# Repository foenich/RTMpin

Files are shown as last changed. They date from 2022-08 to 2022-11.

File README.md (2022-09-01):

# RTMpin
This is a pinball project.

A Rollergames playfield was turned into a hybrid pinball machine (pinball firmware via PinMAME like in virtual pinball, but with real playfield and steel balls).

The emulator PinMAME runs on a Raspberry Pi and controls sound, DMD and a few IO-boards underneath the playfield. These in turn read the switch positions and activates the coils and lamps.

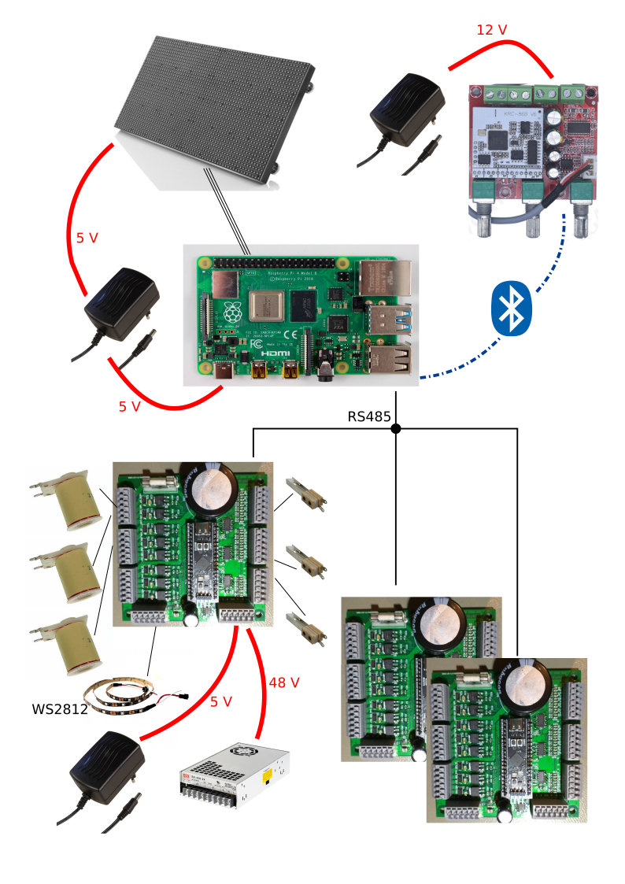
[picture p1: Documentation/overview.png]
overview


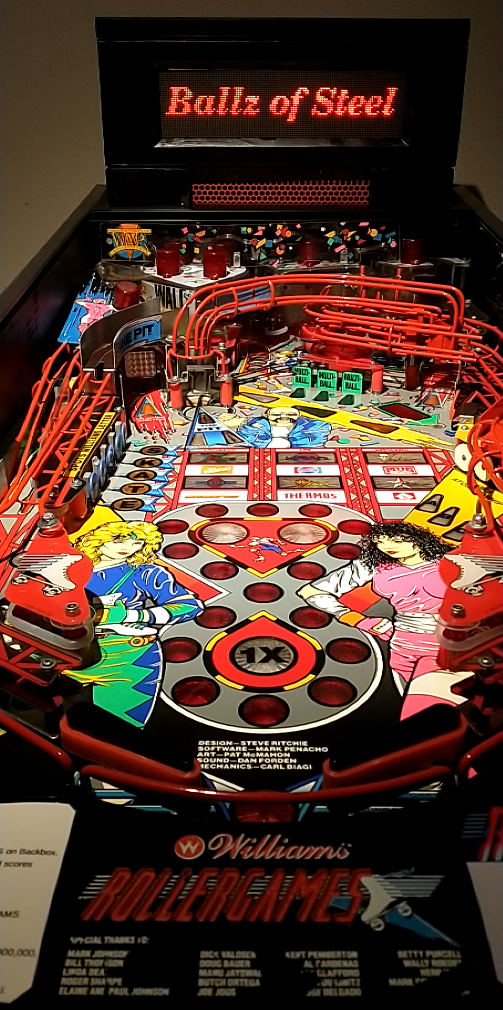
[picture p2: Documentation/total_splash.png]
Playfield and DMD


To watch a video see documentation folder: rg1stgame.mp4

A word of warning: this is a private, non commercial hobby project. Hardware and software still has errors (see issues and Changes.txt). To make use of anything of this project a basic understanding of electronics and programming is necessary. Nothing of it is "plug and play". I'm surely not liable for any damage to assemblies, pinball machines or even persons.

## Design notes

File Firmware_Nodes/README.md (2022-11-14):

# Firmware for IO boards
Firmware is written and compiled with STM32CubeIDE.

For now every node has it's own firmware: 3 nodes -> 3 firmware folders. As different machines can be run on the same playfield (and therefore the same nodes) an extra subdirectory was created for every machine. (e.g. RollerGames for the RG playfield with the RG game-code. Additionally the JudgeDredd_on_RollerGames for the RG playfield with the JD game-code and mapping)

Another folder contains the bootloader firmware witch is the same for all nodes.

Furthermore there are Python (V3) scripts for updating the nodes from the Raspberry Pi.

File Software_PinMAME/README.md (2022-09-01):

# Software related to PinMAME
A few files from the PinMAME project were adapted to communicate with the IO-boards (mainly s11.c).

Here is the link to the branch RTMpin (forked from PinMAME-Version of 5th of April 2021) and added neccessary changes for RTMPin  
https://github.com/foenich/pinmame/tree/RTMpin

Here is the link to the PinMAME project:  
[https://github.com/vpinball/pinmame](https://github.com/vpinball/pinmame)  

To make the DMD (Dot Matrix Display) running the excellent and well documentated library rpi-rgb-led-matrix was used:  
[https://github.com/hzeller/rpi-rgb-led-matrix](https://github.com/hzeller/rpi-rgb-led-matrix)  
To compile the RTMpin branch of PinMAME you also have to compile the rpi-rgb-led-matix library and make it visible to the system (e.g. copy librgbmatrix.so.1 and/or librgbmatrix.a to /usr/local/lib and run ldconfig)

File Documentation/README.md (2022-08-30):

# Technical Description RTMpin

## Overview
The emulator PinMAME runs on a Raspberry Pi and controls sound, DMD and a few IO-boards underneath the playfield. These in turn read the switch positions and activates the coils and lamps.

overview

## Electronics
The heart is a Raspberry Pi 4, which is connected to:
* LED-Matrix (DMD) via the digital I/O pins of the Raspi. 
* Audio amplifier via Bluetooth
* IO boards (nodes, underneath the board) via serial bus connection RS485

The LED matrix is a purchased part, as is the audio amplifier (Class D, 2 x 15 W for speakers in the backbox plus 30 W for the subwoofer in the cabinet). The IO-boards (nodes) are selfmade.

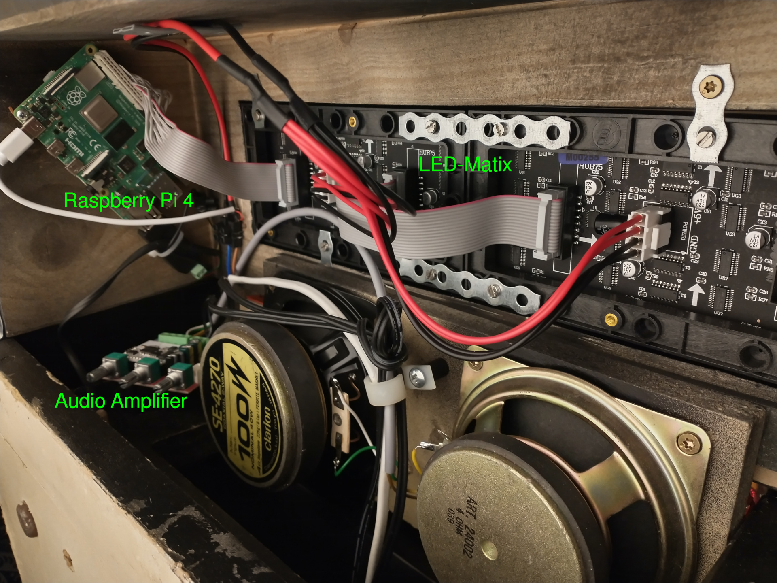
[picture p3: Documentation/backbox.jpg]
backbox


### IO-boards (nodes)
Each of the IO-boards (IO stands for Input/Output) can switch 8 high current outputs, read 18 inputs (direct inputs, no matrix circuitry) and drive a LED strip with WS2812 RGB LEDs. This is used to do all the lights under the playfield and the GI. For the Rollergames 3 IO-boards were necessary (actually 4 would be necessary, but to save a node I did it without the 3 control buttons for the menu navigation. At the moment I make these settings on the computer and then copy the corresponding file to the Raspberry. Maybe I'll add the switches to the IO's of the Raspberry, if I miss them).

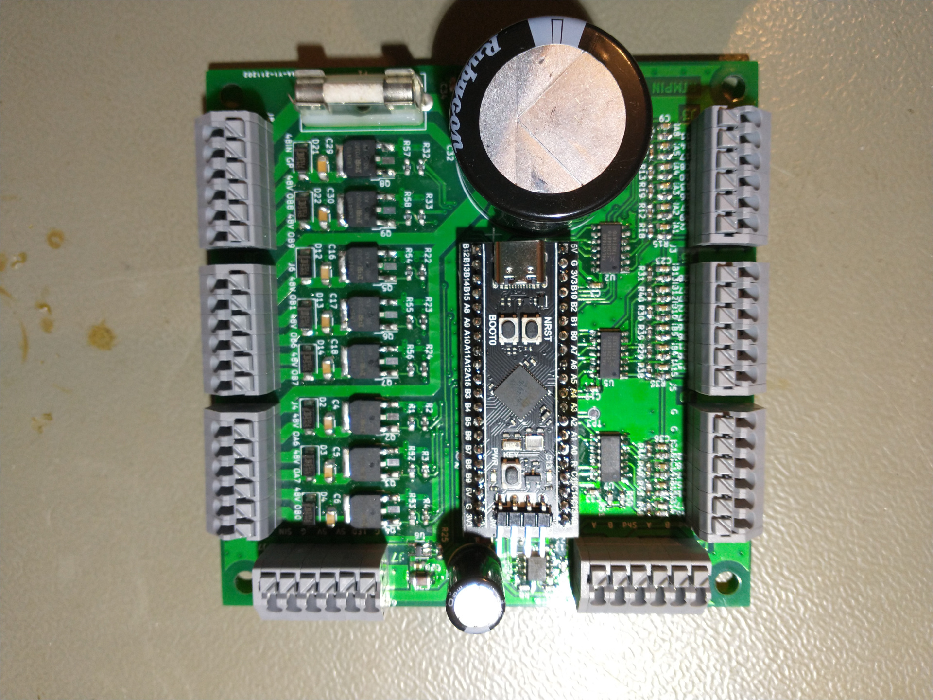
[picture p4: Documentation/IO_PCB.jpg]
Node


The control of the inputs and outputs and the communication with the Raspberry Pi is done by a STM32F401. I used a small board (Blackpill) for this, because it was better available than the microcontrollers themselvs (they were not at all available when I developed the board).

### Data communication
For communication with the Raspberry Pi I decided to use the serial bus connection RS485 (half duplex, 115 kbit/s). This is very robust (resistant to electro magnetic interference, EMI) and requires only two lines (plus a reference ground if necessary).

### Wiring
The wiring of the lamps is quite straightforward, since all LEDs have a small controller on board, which takes it's data packet from the serial data stream and passes the rest on to the next LED. Therefore only one wire for the data plus two wires for the power supply are needed.

For the wiring to the coils I used a 2-wire line per coil. This has significant advantages for electromagnetic compatibility (EMC), because the forward and return conductors are close to each other and thus emit less interference. Due to the distributed nodes on the bottom side of the board, the overall wiring is "mostly harmless".

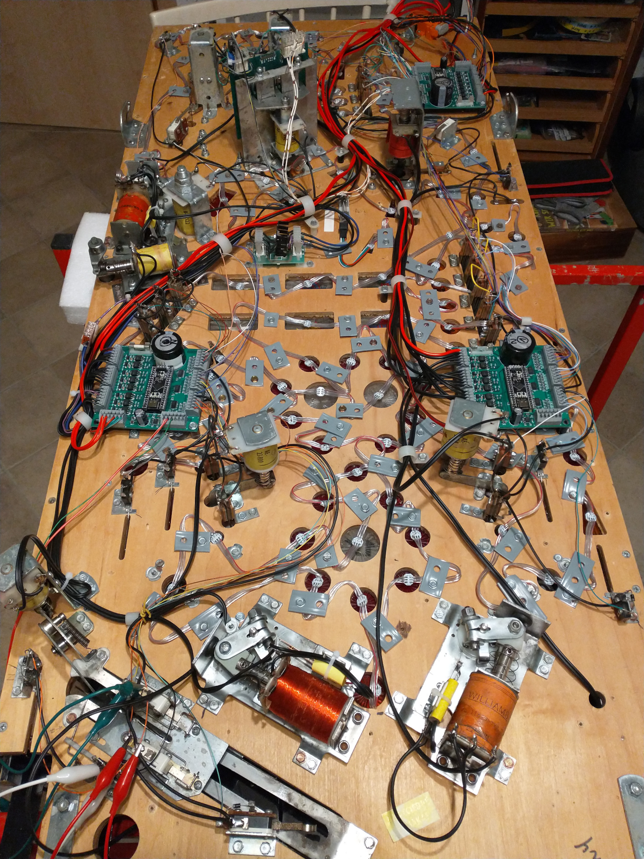
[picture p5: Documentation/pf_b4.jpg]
Overall wiring


### Power supply
The power supply for the components is made by 4 purchased power supplies:
* 5 V, 2.5 A for Raspi and DMD.
* 5 V, 2.5 A for node electronics and lamps
* 48 V, 7.3 A for the coils and flasher
* 12 V, 2 A for audio (I don't need the full power of the amplifier)

The two 5 V power supplies could be combined by a stronger single power supply, but I already had the wall power supplys at home, so they were used.

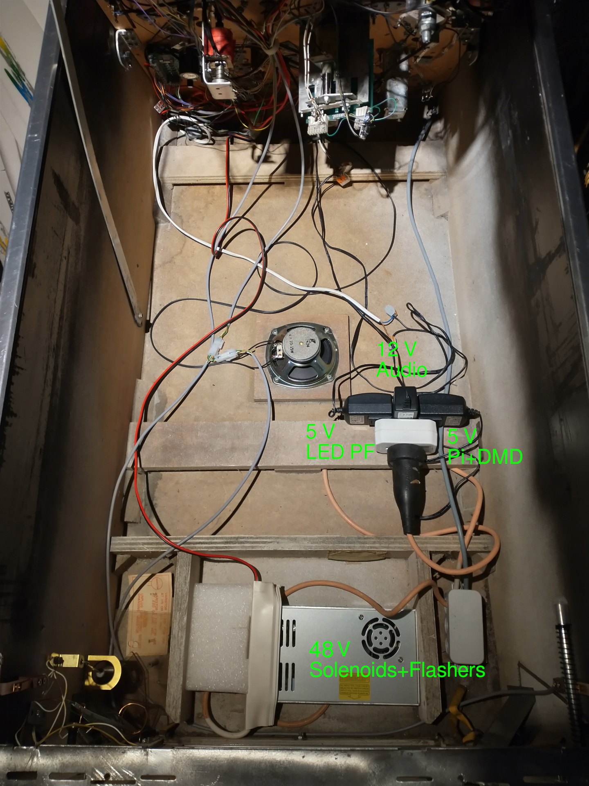
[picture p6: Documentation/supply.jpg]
power supply


## Software
### PinMAME
The linchpin of the software is the pinball emulator PinMAME:  
[https://github.com/vpinball/pinmame](https://github.com/vpinball/pinmame)  
The development team did a great job here and even ported the software to Linux, which makes it possible to control the pinball via a Raspberry Pi in the first place.

The pinball emulator runs on the Raspberry Pi 4 under a headless Linux (Raspberry Pi OS Lite). I had to make some adjustments to PinMAME for controlling the DMD and communicating with my IO boards (which lamps and coils are currently active and also for reading back the current switch states). 

### RPI RGB LED matrix
To control the DMD I used the excellent and well documented library from H. Zeller:  
[https://github.com/hzeller/rpi-rgb-led-matrix](https://github.com/hzeller/rpi-rgb-led-matrix)

### Firmware for IO boards
The software for the nodes was created with the development environment from ST Microelectronics for the STM32 family in C programming language. This went quite well, but as it was only a "prove of concept", I hardcoded many parameters and structured the code as simple as possible. I paid special attention to short interrupt routines and continuous (without waiting times) loop-based instruction sequences (similar to PLC programming). This is the only way to achieve the fast data sequences (almost 1 MHz) for the LED strips, which must be done in parallel to the RS485 transmission (115 kBaud) and in parallel to the IO control.

About all 60 ms the IOs (inputs and outputs) are updated by PinMAME. This is too slow for some functions. Therefore e.g. the flippers, bumpers and sling shots are controlled directly by the nodes. Here the delay time is shorter than one millisecond and therefore negligible.

All coils and flashers are powered with 48 V, so I only need one power supply for the power outputs. However, not all coils (and certainly not the flashers) are designed for 48 V, so all outputs are pulse width modulated (PWM). Therefore the time-averaged (and thus relevant) supply voltage for each coil and flasher can be adjusted individually.

The software for the IO boards can be updated directly from the Raspberry Pi. To do this, you can log in remotely (via ssh) to the Raspberry Pi and then start the software update. Very convenient - in my opinion - since you don't even have to open the pinball machine. The only data connection from the Raspi to the nodes is the RS485 bus. So the software update has to run over it, too. The process and the data transfer on the Raspberry side was realized via Python scripts.

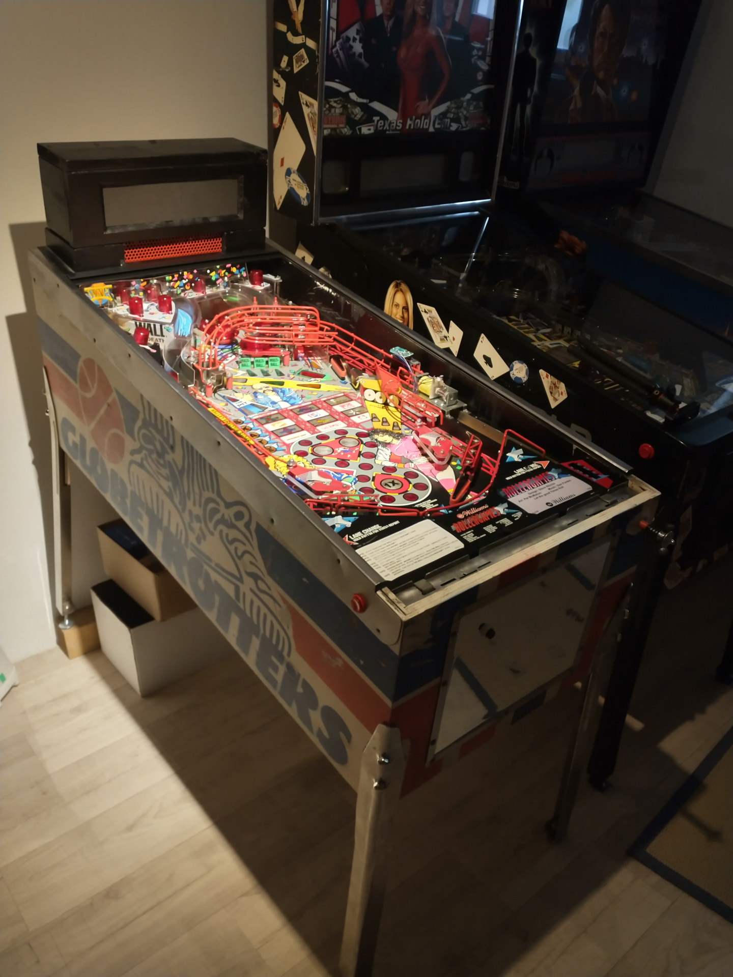
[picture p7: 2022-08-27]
Documentation/total_side.jpg

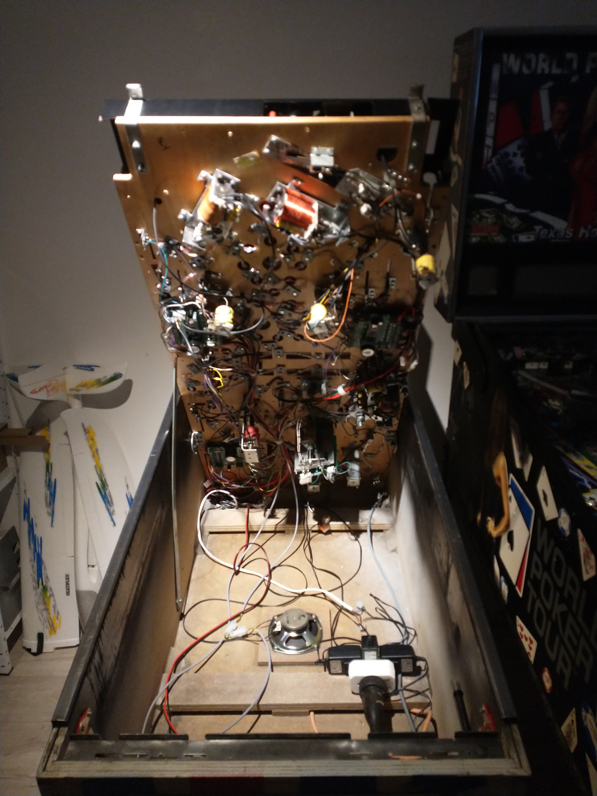
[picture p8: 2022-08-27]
Documentation/open.jpg

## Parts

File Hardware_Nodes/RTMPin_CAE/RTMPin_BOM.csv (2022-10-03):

Reference | Quantity | Value | Footprint | Datasheet
C10 C15 C28 | 3 | 10u 25V | Capacitor_SMD:C_1206_3216Metric | ~
C1 C2 C3 C7 C8 C9 C11 C12 C13 C14 C19 C20 C21 C22 C23 C25 C26 C27 C31 C33 C35 C36 C37 C38 C39 C40 | 26 | 100n | Capacitor_SMD:C_0603_1608Metric | ~
C24 | 1 | 1000µ 10V | Capacitor_THT:CP_Radial_D10.0mm_P5.00mm | ~
C4 C5 C6 C16 C17 C18 C29 C30 | 8 | 470p 500V | Capacitor_SMD:C_1206_3216Metric | ~
C32 | 1 | 3300µ 63V | Capacitor_THT:CP_Radial_D30.0mm_P10.00mm_SnapIn | ~
C34 | 1 | 100n 50V | Capacitor_SMD:C_0603_1608Metric | ~
D2 D3 D4 D12 D13 D14 D21 D22 | 8 | MRA4004T3G | Diode_SMD:D_SMA | http://www.onsemi.com/pub_link/Collateral/MRA4003T3-D.PDF
D6 D7 D8 D9 D10 D11 D15 D16 D17 D18 D19 D20 D24 D25 D27 D28 D29 D30 | 18 | SD05 | Diode_SMD:D_SOD-323 | ~
D26 | 1 | SMAJ48 | Diode_SMD:D_SMA | ~
D1 D5 | 2 | SD15 | Diode_SMD:D_SOD-323 | ~
F1 | 1 | T6A | Fuse:Fuseholder_Cylinder-5x20mm_Schurter_0031_8201_Horizontal_Open | ~
J2 J3 J4 J5 J6 J7 J8 J9 | 8 | Conn_01x06 | RTMPin_CAE:Terminal_Block_RTMPin | ~
Q2 Q3 Q4 Q5 Q6 Q7 Q8 Q9 | 8 | IRLR3410 | Package_TO_SOT_SMD:TO-252-3_TabPin4 | ~
R2 R3 R4 R21 R22 R23 R24 R25 R32 R33 R50 R51 | 12 | 10k | Resistor_SMD:R_0603_1608Metric | ~
R12 R13 R14 R18 R19 R20 R29 R30 R31 R38 R39 R40 R43 R44 R48 R49 | 16 | 2k2 | Resistor_SMD:R_0603_1608Metric | ~
R1 R5 R9 R10 R11 R15 R16 R17 R26 R27 R28 R35 R36 R37 R41 R42 R45 R46 R47 R52 R53 R54 R55 R56 R57 R58 | 26 | 100R | Resistor_SMD:R_0603_1608Metric | ~
R6 R8 | 2 | 1k | Resistor_SMD:R_0603_1608Metric | ~
R7 | 1 | 120R | Resistor_SMD:R_0603_1608Metric | ~
TP2 TP3 | 2 | TestPoint | TestPoint:TestPoint_Pad_D1.5mm | ~
U3 | 1 | ADM3483 | Package_SO:SOIC-8_3.9x4.9mm_P1.27mm | http://www.icbase.com/pdf/SPX/SPX00480106.pdf
U4 | 1 | BlackPill STM32F4xx | Package_DIP:DIP-40_W15.24mm_Socket_LongPads
U2 U5 U7 | 3 | SN74LVC14A | Package_SO:SO-14_3.9x8.65mm_P1.27mm | http://www.ti.com/lit/gpn/sn74LV14
U6 | 1 | SN74AHCT1G125 | Package_TO_SOT_SMD:SOT-23-5

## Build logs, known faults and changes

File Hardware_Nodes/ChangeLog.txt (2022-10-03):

-----------V0.1.1------------------------------------------------------
changed pads form handsolder to standard
Rx/Tx corrected (swaped)
moved C24 a bit to the right (access for USB-connector)
moved U4 up (BlackPill exaggerates the DIP-Socket at the bottom side an conflicts with C32)
pull down instead of a pull up at nRE/DE of RS485
bigger mounting holes
moved all part to top side
changed TVS to unipolar

-----------V0.1.0------------------------------------------------------
first shot

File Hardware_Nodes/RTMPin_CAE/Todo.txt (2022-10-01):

# Todos for next version:
* U2, U5, U7: may use a different housing for 74LVC14 (e.g. TSSOP14), because better available

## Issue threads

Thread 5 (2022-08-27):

Plug in connectors

foenich, 2022-08-27:
More convenient when node needs to be replaced.

foenich, 2022-11-13:
Layout is ready for plug in connectors eg. from Phoenix. Just mount them ;-)

Closed 2022-11-13.

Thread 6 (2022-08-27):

Electronic fuse for power outputs

foenich, 2022-08-27:

foenich, 2022-11-13:
Will not be done, as too expensive and problems with availability (eg. 2 € for ACS711).

Closed 2022-11-13.

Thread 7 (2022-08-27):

Protect 5 V circuits from 48 V

foenich, 2022-08-27:
In case of wrong wiring.

foenich, 2022-11-13:
Additional fuse required. Will not be done within this project (maybe in PPUC project), as new layout would be required. Workaround: use external fuse for 5 V supply.

Closed 2022-11-13.

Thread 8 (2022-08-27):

Parameter settings per webserver

foenich, 2022-08-27:
e.g. solenoid power, LED color, LED brightness

foenich, 2022-11-13:
Will be done within PPUC project.

foenich, 2022-11-13:
Will be done within PPUC project.

Closed 2022-11-13.

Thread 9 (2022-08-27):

Update node while other nodes running

foenich, 2022-08-27:
Update only works if other nodes are in reset (manually press reset) after update process started.

foenich, 2022-11-14:
Strange behavior: the A12 GPIO (direction of RS485) goes high during pressing the reset button, even if it is pulled low by an external 10k.
Routine for "update other node" was never reached as no "rxBufferUpdated" happens if other node is addressed. -> removed rxBufferUpdated in the if clause and only check for nodeStatus == 3.

Closed 2022-11-14.

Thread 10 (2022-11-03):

Debounce Flipperbuttons

foenich, 2022-11-03:
Bouncing buttons cause loss in flipperfinger power

foenich, 2022-11-14:
bouncing time: max. 5 ms (measured), from these max. 2 ms off at a stretch. Shortest time button pressed I archived was 7 ms -> added a minimum on time of 5 ms for the flipper solenoid

Closed 2022-11-14.

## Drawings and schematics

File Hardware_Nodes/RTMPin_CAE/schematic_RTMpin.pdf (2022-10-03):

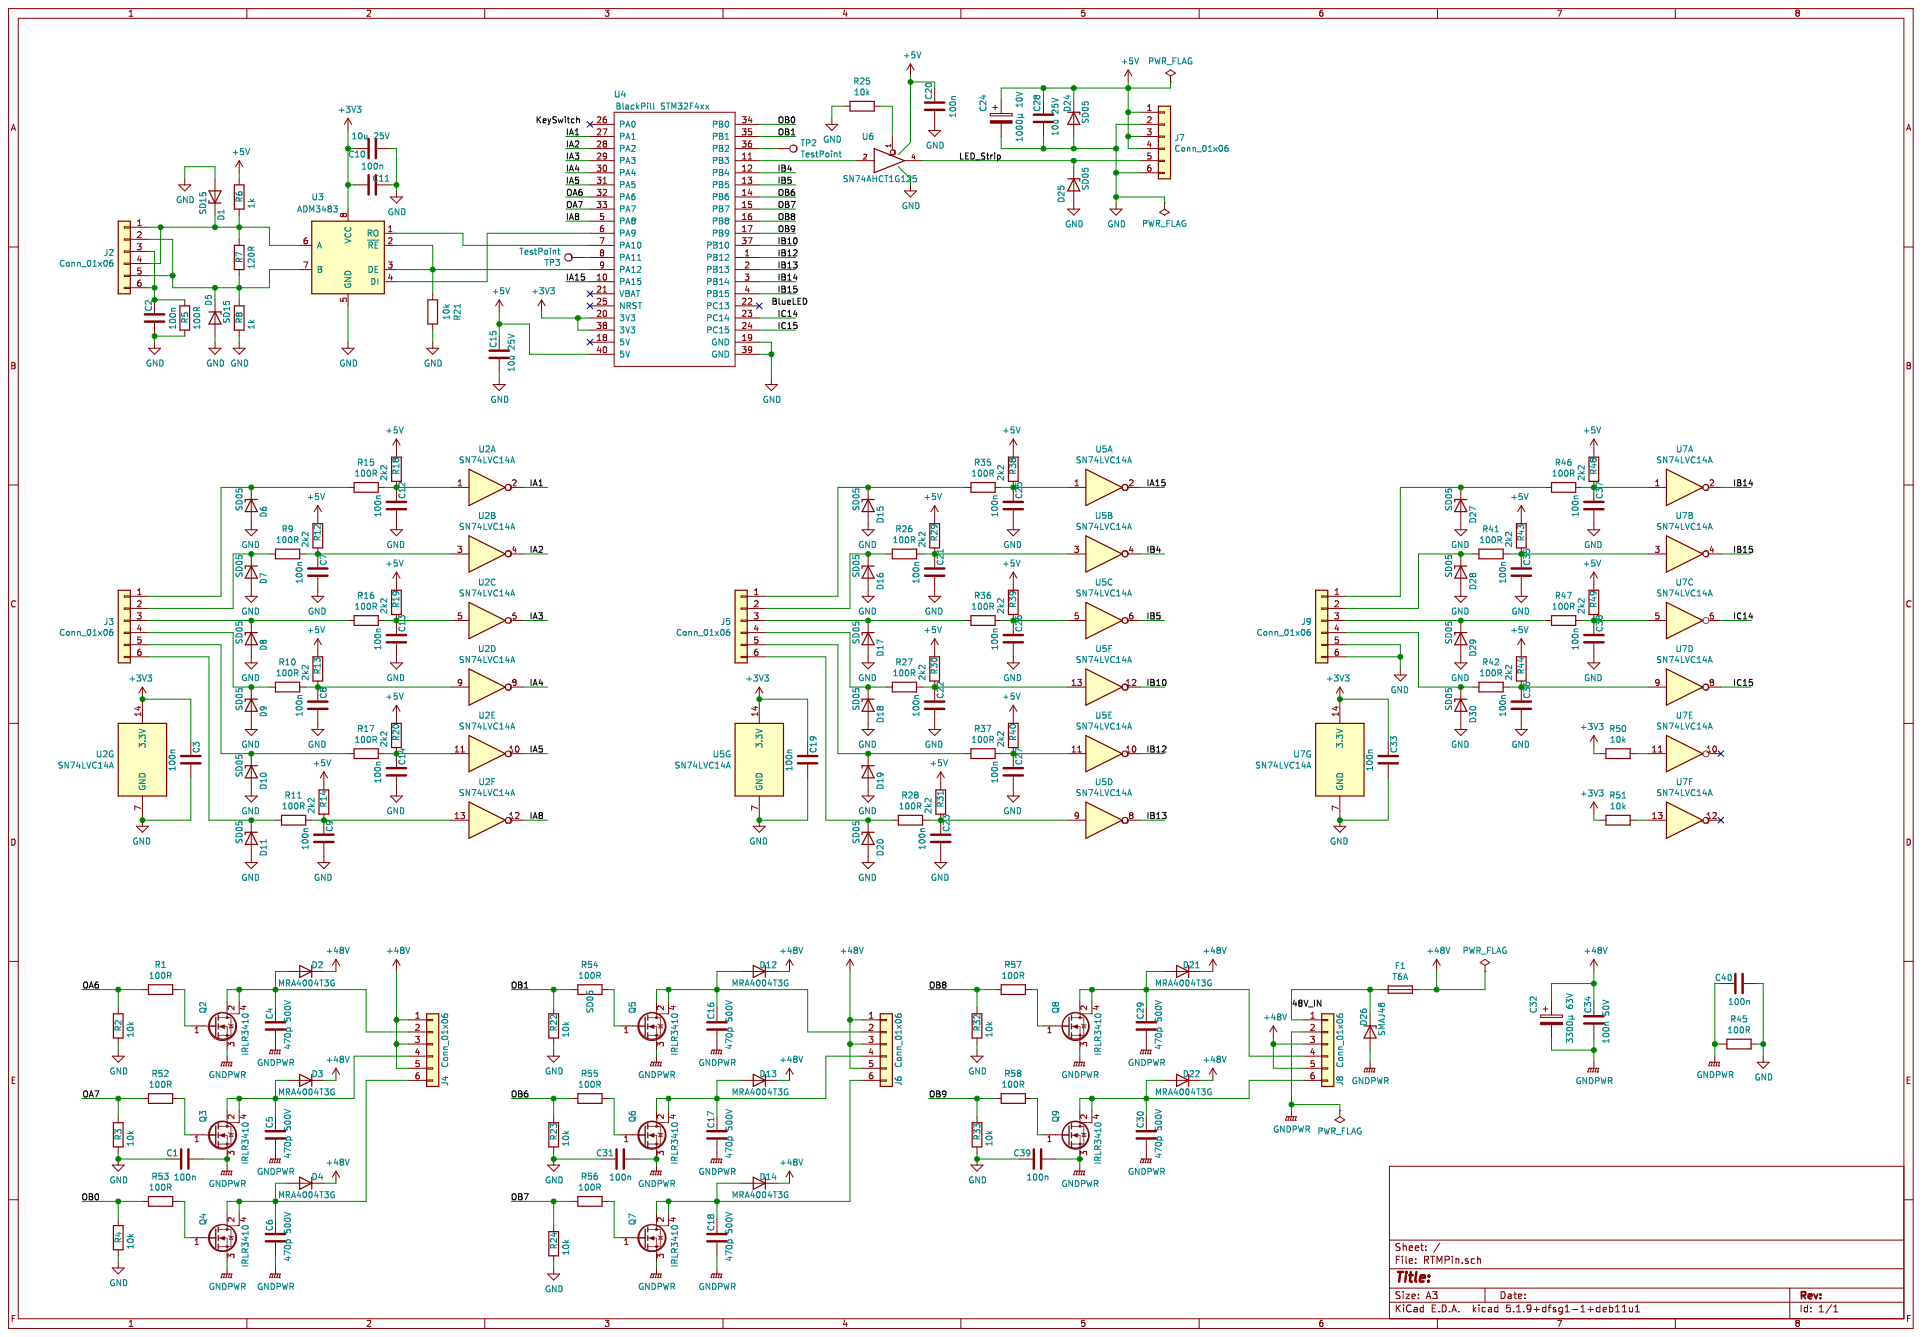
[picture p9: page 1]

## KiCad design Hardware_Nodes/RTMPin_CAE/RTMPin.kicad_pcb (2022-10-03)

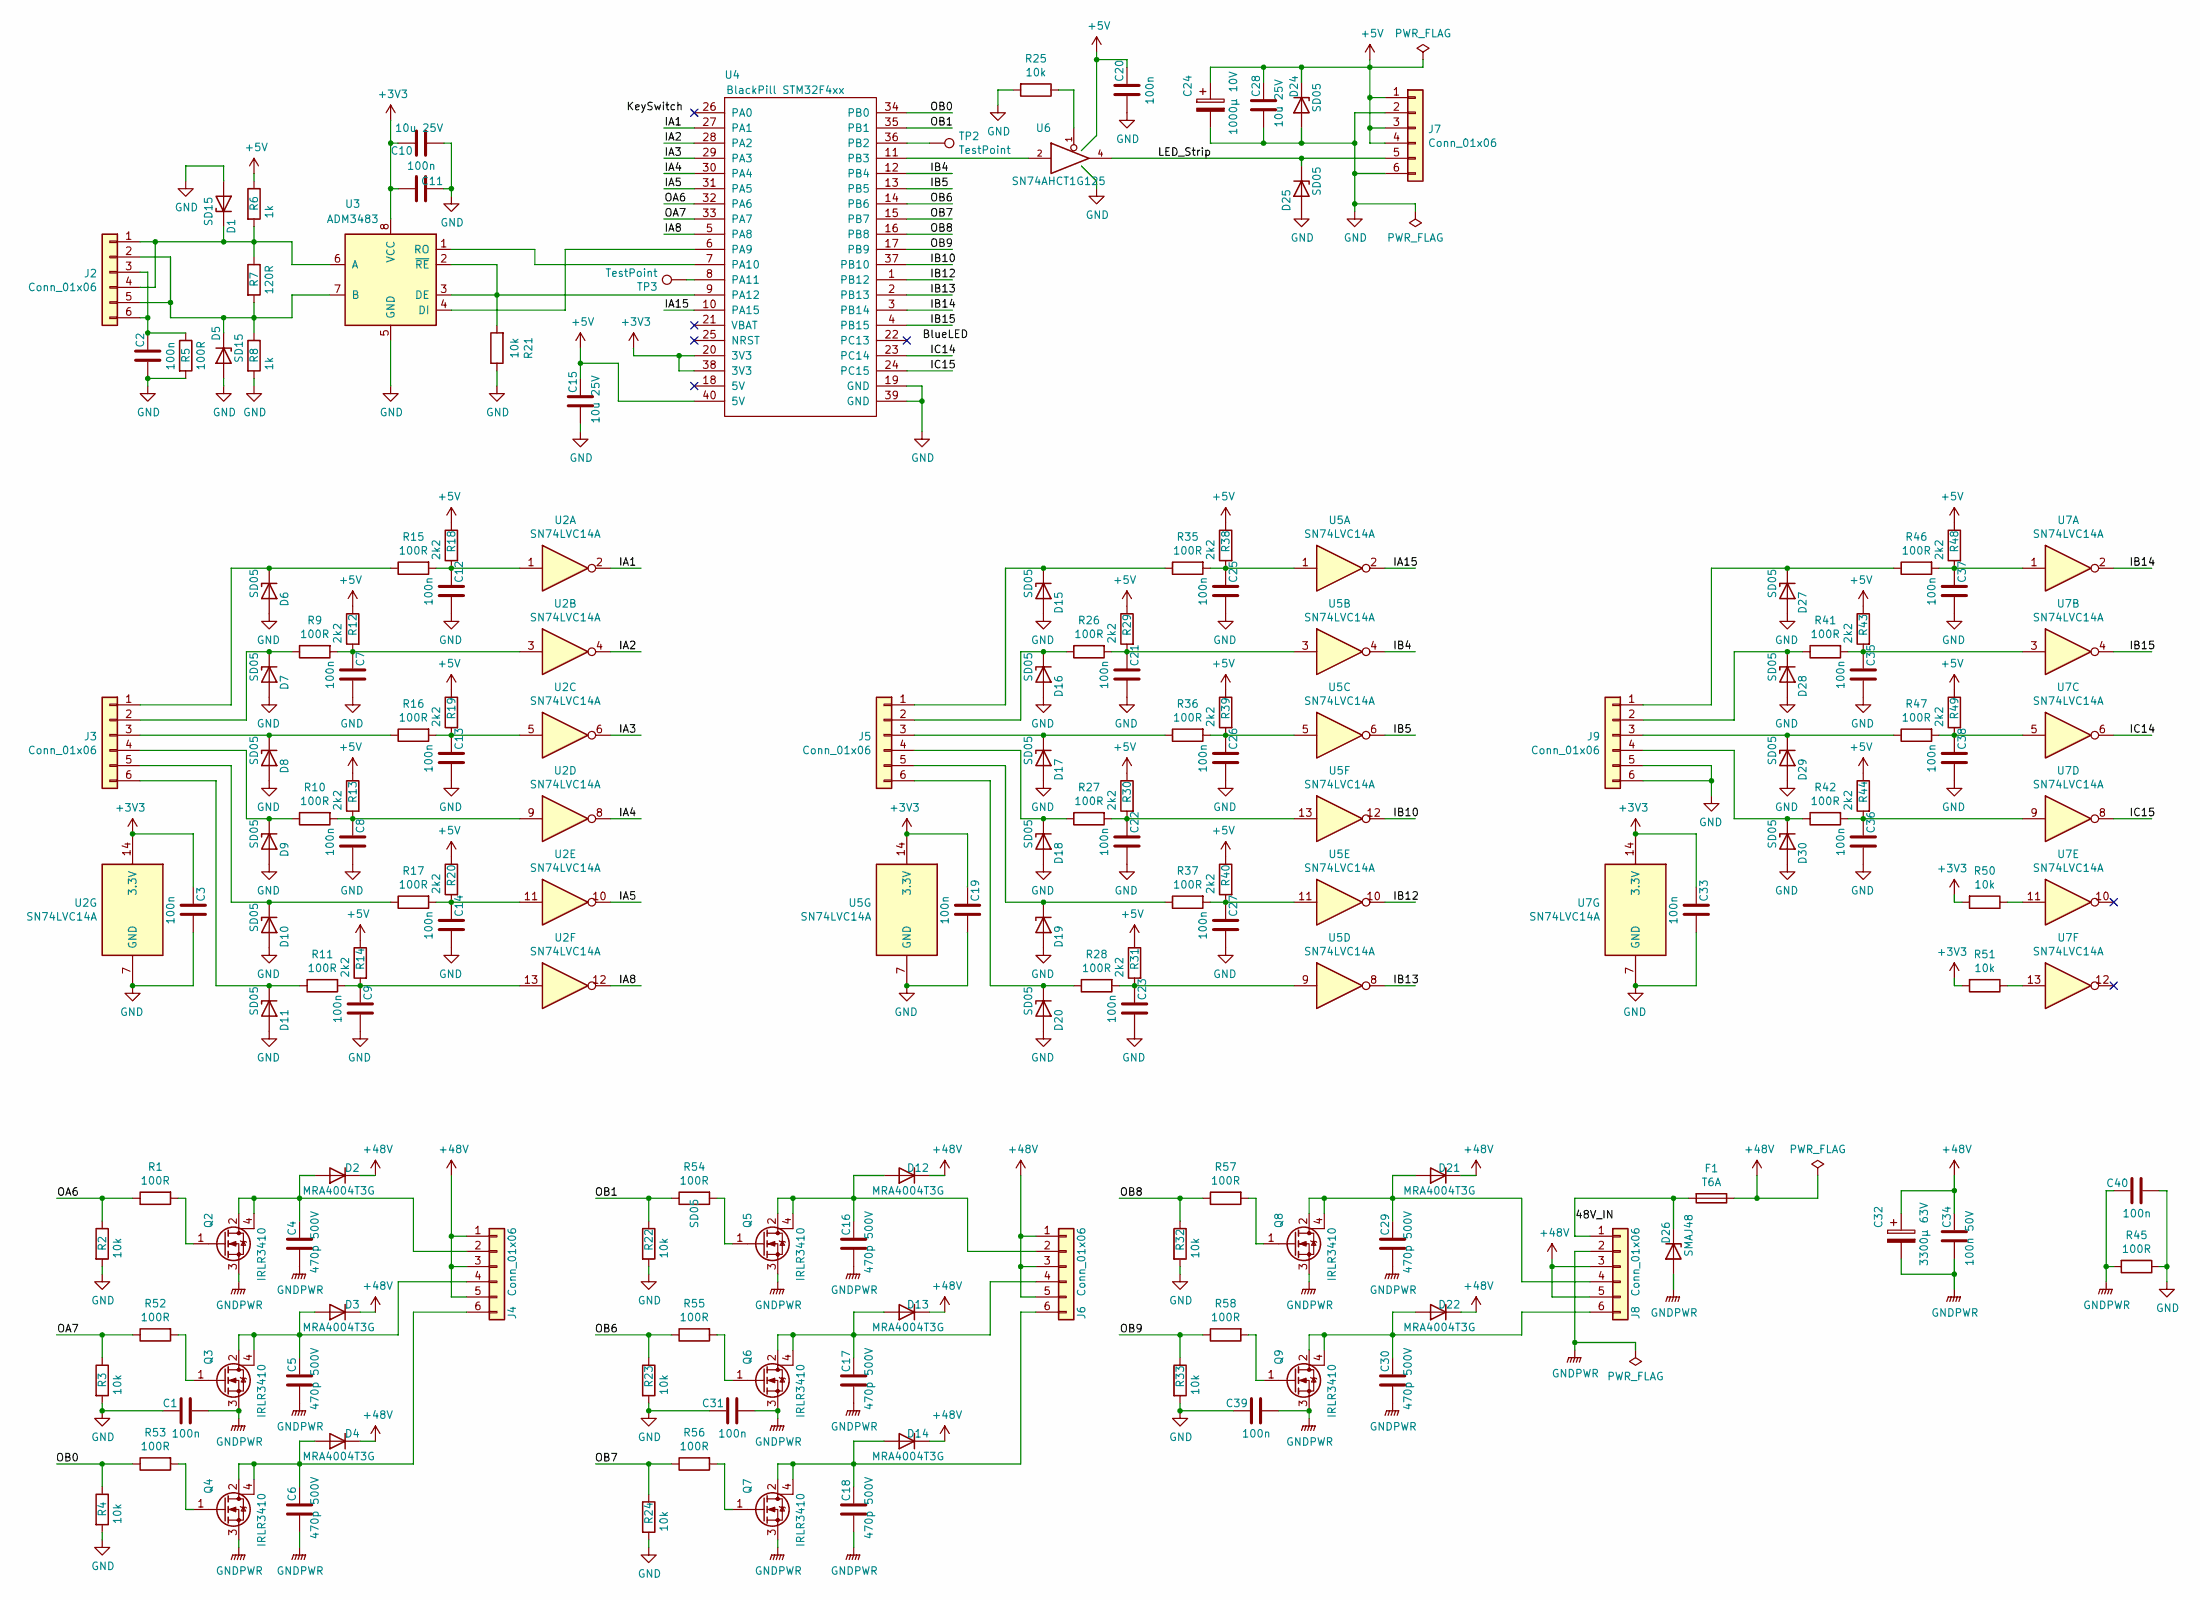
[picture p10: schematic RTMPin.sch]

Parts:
C1, C2, C3, C7, C8, C9, C11, C12, C13, C14, C19, C20, C21, C22, C23, C25, C26, C27, C31, C33, C35, C36, C37, C38, C39, C40: 100n; C_0603_1608Metric
C4, C5, C6, C16, C17, C18, C29, C30: 470p 500V; C_1206_3216Metric
C10, C15, C28: 10u 25V; C_1206_3216Metric
C24: 1000µ 10V; CP_Radial_D10.0mm_P5.00mm
C32: 3300µ 63V; CP_Radial_D30.0mm_P10.00mm_SnapIn
C34: 100n 50V; C_0603_1608Metric
D1, D5: SD15; D_SOD-323
D2, D3, D4, D12, D13, D14, D21, D22: MRA4004T3G; D_SMA
D6, D7, D8, D9, D10, D11, D15, D16, D17, D18, D19, D20, D24, D25, D27, D28, D29, D30: SD05; D_SOD-323
D26: SMAJ48; D_SMA
F1: T6A; Fuseholder_Cylinder-5x20mm_Schurter_0031_8201_Horizontal_Op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
J2, J3, J4, J5, J6, J7, J8, J9: Conn_01x06; Terminal_Block_RTMPin
Q2, Q3, Q4, Q5, Q6, Q7, Q8, Q9: IRLR3410; TO-252-3_TabPin4
R1, R5, R9, R10, R11, R15, R16, R17, R26, R27, R28, R35, R36, R37, R41, R42, R45, R46, R47, R52, R53, R54, R55, R56, R57, R58: 100R; R_0603_1608Metric
R2, R3, R4, R21, R22, R23, R24, R25, R32, R33, R50, R51: 10k; R_0603_1608Metric
R6, R8: 1k; R_0603_1608Metric
R7: 120R; R_0603_1608Metric
R12, R13, R14, R18, R19, R20, R29, R30, R31, R38, R39, R40, R43, R44, R48, R49: 2k2; R_0603_1608Metric
TP2, TP3: TestPoint; TestPoint_Pad_D1.5mm
U2, U5, U7: SN74LVC14A; SO-14_3.9x8.65mm_P1.27mm
U3: ADM3483; SOIC-8_3.9x4.9mm_P1.27mm
U4: BlackPill STM32F4xx; DIP-40_W15.24mm_Socket_LongPads
U6: SN74AHCT1G125; SOT-23-5

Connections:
+3V3: C3.1, C10.1, C11.1, C19.1, C33.1, R50.2, R51.2, U2.14 (3.3V), U3.8 (VCC), U4.20 (3V3), U4.38 (3V3), U5.14 (3.3V), U7.14 (3.3V)
+5V: C15.1, C20.1, C24.1, C28.1, D24.1 (K), J7.1, J7.3, J7.4, R6.1, R12.1, R13.1, R14.1, R18.1, R19.1, R20.1, R29.1, R30.1, R31.1, R38.1, R39.1, R40.1, R43.1, R44.1, R48.1, R49.1, U4.40 (5V), U6.5 (VCC)
+48V: C32.1, C34.1, D2.1 (K), D3.1 (K), D4.1 (K), D12.1 (K), D13.1 (K), D14.1 (K), D21.1 (K), D22.1 (K), F1.1, J4.1, J4.3, J4.5, J6.1, J6.3, J6.5, J8.3, J8.5
/48V_IN: D26.1 (K), F1.2, J8.1
/IA1: U2.2, U4.27 (PA1)
/IA2: U2.4, U4.28 (PA2)
/IA3: U2.6, U4.29 (PA3)
/IA4: U2.8, U4.30 (PA4)
/IA5: U2.10, U4.31 (PA5)
/IA8: U2.12, U4.5 (PA8)
/IA15: U4.10 (PA15), U5.2
/IB4: U4.12 (PB4), U5.4
/IB5: U4.13 (PB5), U5.6
/IB10: U4.37 (PB10), U5.12
/IB12: U4.1 (PB12), U5.10
/IB13: U4.2 (PB13), U5.8
/IB14: U4.3 (PB14), U7.2
/IB15: U4.4 (PB15), U7.4
/IC14: U4.23 (PC14), U7.6
/IC15: U4.24 (PC15), U7.8
/LED_Strip: D25.1 (K), J7.5, U6.4
/OA6: R1.1, R2.1, U4.32 (PA6)
/OA7: R3.1, R52.1, U4.33 (PA7)
/OB0: R4.1, R53.1, U4.34 (PB0)
/OB1: R22.1, R54.1, U4.35 (PB1)
/OB6: R23.1, R55.1, U4.14 (PB6)
/OB7: R24.1, R56.1, U4.15 (PB7)
/OB8: R32.1, R57.1, U4.16 (PB8)
/OB9: R33.1, R58.1, U4.17 (PB9)
GND: C1.1, C2.2, C3.2, C7.2, C8.2, C9.2, C10.2, C11.2, C12.2, C13.2, C14.2, C15.2, C19.2, C20.2, C21.2, C22.2, C23.2, C24.2, C25.2, C26.2, C27.2, C28.2, C31.1, C33.2, C35.2, C36.2, C37.2, C38.2, C39.1, C40.2, D1.2 (A), D5.2 (A), D6.2 (A), D7.2 (A), D8.2 (A), D9.2 (A), D10.2 (A), D11.2 (A), D15.2 (A), D16.2 (A), D17.2 (A), D18.2 (A), D19.2 (A), D20.2 (A), D24.2 (A), D25.2 (A), D27.2 (A), D28.2 (A), D29.2 (A), D30.2 (A), J7.2, J7.6, J9.5, J9.6, R2.2, R3.2, R4.2, R5.2, R8.2, R21.1, R22.2, R23.2, R24.2, R25.2, R32.2, R33.2, R45.1, U2.7 (GND), U3.5 (GND), U4.19 (GND), U4.39 (GND), U5.7 (GND), U6.3 (GND), U7.7 (GND)
GNDPWR: C1.2, C4.2, C5.2, C6.2, C16.2, C17.2, C18.2, C29.2, C30.2, C31.2, C32.2, C34.2, C39.2, C40.1, D26.2 (A), J8.2, Q2.3 (S), Q3.3 (S), Q4.3 (S), Q5.3 (S), Q6.3 (S), Q7.3 (S), Q8.3 (S), Q9.3 (S), R45.2
unnamed: C2.1, J2.3, J2.6, R5.1
unnamed: C4.1, D2.2 (A), J4.2, Q2.2 (D), Q2.4 (D)
unnamed: C5.1, D3.2 (A), J4.4, Q3.2 (D), Q3.4 (D)
unnamed: C6.1, D4.2 (A), J4.6, Q4.2 (D), Q4.4 (D)
unnamed: C7.1, R9.2, R12.2, U2.3
unnamed: C8.1, R10.2, R13.2, U2.9
unnamed: C9.1, R11.2, R14.2, U2.13
unnamed: C12.1, R15.2, R18.2, U2.1
unnamed: C13.1, R16.2, R19.2, U2.5
unnamed: C14.1, R17.2, R20.2, U2.11
unnamed: C16.1, D12.2 (A), J6.2, Q5.2 (D), Q5.4 (D)
unnamed: C17.1, D13.2 (A), J6.4, Q6.2 (D), Q6.4 (D)
unnamed: C18.1, D14.2 (A), J6.6, Q7.2 (D), Q7.4 (D)
unnamed: C21.1, R26.2, R29.2, U5.3
unnamed: C22.1, R27.2, R30.2, U5.13
unnamed: C23.1, R28.2, R31.2, U5.9
unnamed: C25.1, R35.2, R38.2, U5.1
unnamed: C26.1, R36.2, R39.2, U5.5
unnamed: C27.1, R37.2, R40.2, U5.11
unnamed: C29.1, D21.2 (A), J8.4, Q8.2 (D), Q8.4 (D)
unnamed: C30.1, D22.2 (A), J8.6, Q9.2 (D), Q9.4 (D)
unnamed: C35.1, R41.2, R43.2, U7.3
unnamed: C36.1, R42.2, R44.2, U7.9
unnamed: C37.1, R46.2, R48.2, U7.1
unnamed: C38.1, R47.2, R49.2, U7.5
unnamed: D1.1 (K), J2.1, J2.4, R6.2, R7.1, U3.6 (A)
unnamed: D5.1 (K), J2.2, J2.5, R7.2, R8.1, U3.7 (B)
unnamed: D6.1 (K), J3.1, R15.1
unnamed: D7.1 (K), J3.2, R9.1
unnamed: D8.1 (K), J3.3, R16.1
unnamed: D9.1 (K), J3.4, R10.1
unnamed: D10.1 (K), J3.5, R17.1
unnamed: D11.1 (K), J3.6, R11.1
unnamed: D15.1 (K), J5.1, R35.1
unnamed: D16.1 (K), J5.2, R26.1
unnamed: D17.1 (K), J5.3, R36.1
unnamed: D18.1 (K), J5.4, R27.1
unnamed: D19.1 (K), J5.5, R37.1
unnamed: D20.1 (K), J5.6, R28.1
unnamed: D27.1 (K), J9.1, R46.1
unnamed: D28.1 (K), J9.2, R41.1
unnamed: D29.1 (K), J9.3, R47.1
unnamed: D30.1 (K), J9.4, R42.1
unnamed: Q2.1 (G), R1.2
unnamed: Q3.1 (G), R52.2
unnamed: Q4.1 (G), R53.2
unnamed: Q5.1 (G), R54.2
unnamed: Q6.1 (G), R55.2
unnamed: Q7.1 (G), R56.2
unnamed: Q8.1 (G), R57.2
unnamed: Q9.1 (G), R58.2
unnamed: R21.2, U3.2 (~RE~), U3.3 (DE), U4.9 (PA12)
unnamed: R25.1, U6.1
unnamed: R50.1, U7.11
unnamed: R51.1, U7.13
unnamed: TP2.1, U4.36 (PB2)
unnamed: TP3.1, U4.8 (PA11)
unnamed: U3.1 (RO), U4.7 (PA10)
unnamed: U3.4 (DI), U4.6 (PA9)
unnamed: U4.11 (PB3), U6.2

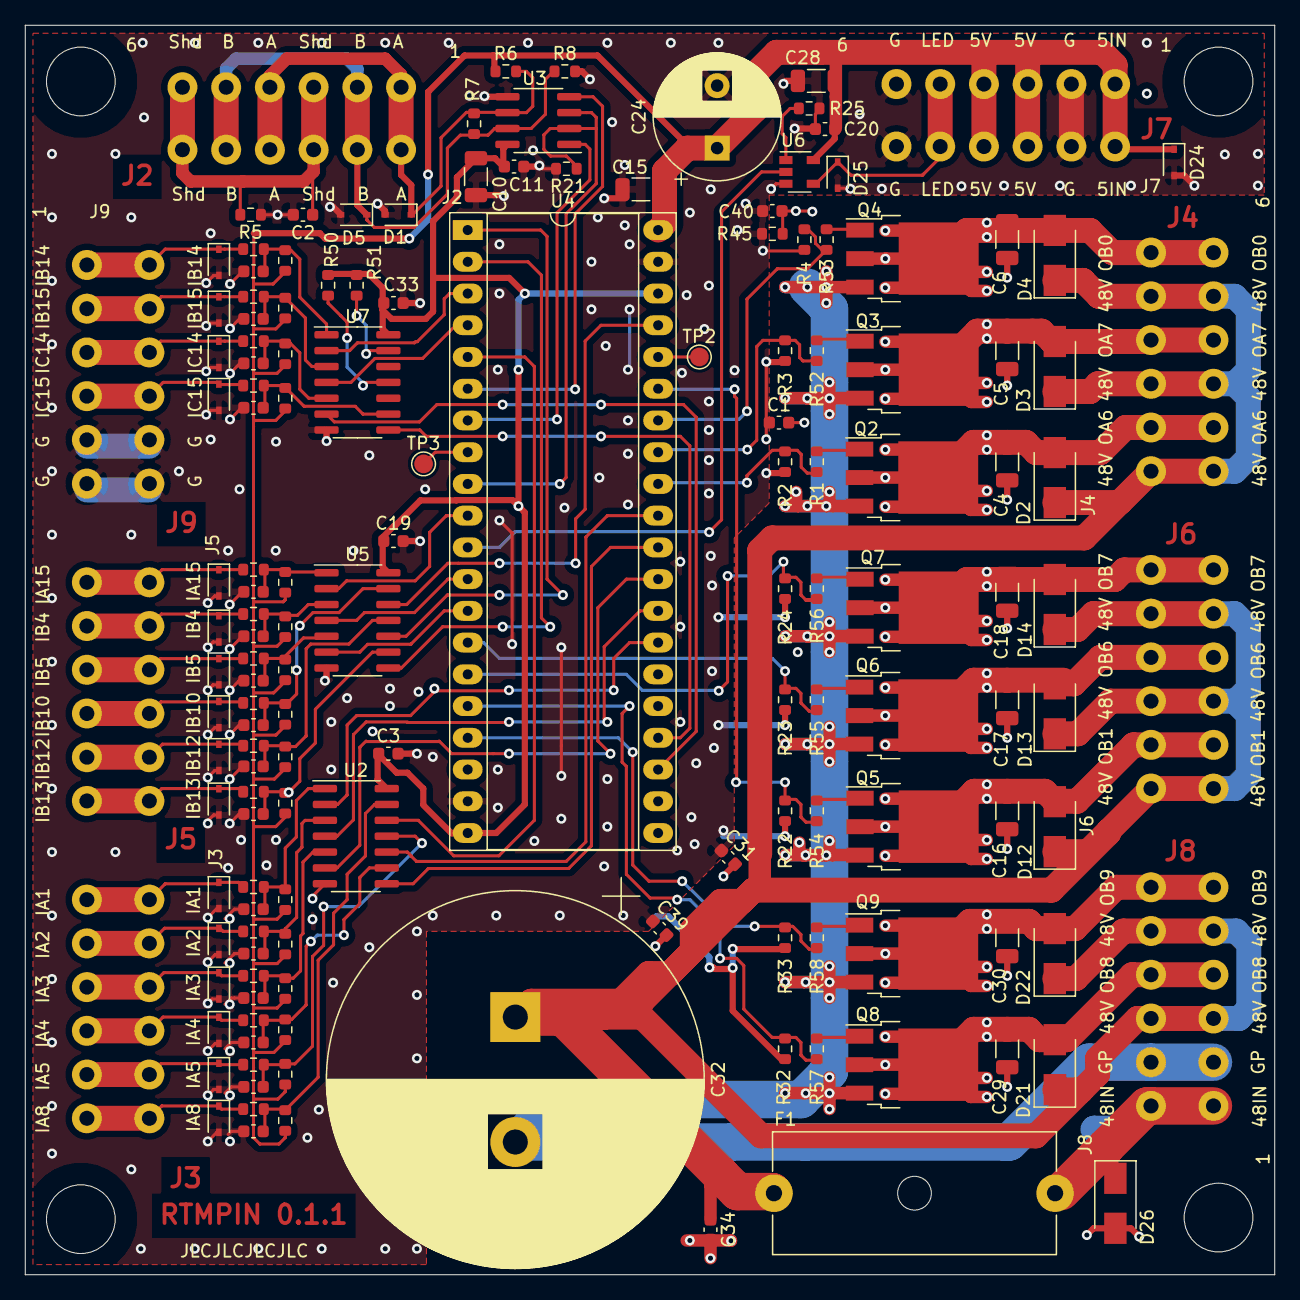
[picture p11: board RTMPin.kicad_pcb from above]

Board: 2 copper layers, 100.0 x 100.0 mm, 151 parts (0 on the bottom side), 91 nets.

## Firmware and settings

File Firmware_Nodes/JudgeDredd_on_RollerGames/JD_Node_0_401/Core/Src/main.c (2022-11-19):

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
/* Includes ------------------------------------------------------------------*/
#include "main.h"

CRC_HandleTypeDef hcrc;

/* USER CODE BEGIN PV */
uint8_t dataArrived = 0;
uint8_t currentRx = 0;

static uint32_t tmp_led_data[2*3*8];
static uint32_t current_led;        /*!< Current LED number we are sending */

uint32_t led[NR_OF_LEDS]; /* holds the color (0xWWRRGGBB) of all LEDs */

uint8_t rxBuffer[17]; /* addr&length + data (max 16) */
uint8_t rxBufferUpdated; /* new frame complete */
uint8_t nodeStatus; /*        * 0 -> standard (receiving) operation
                              * 1 -> send data to Pi
                              * 2 -> Software update of this node
                              * 3 -> Software update of other nodes */

/* USER CODE END PV */

void SystemClock_Config(void);
static void MX_GPIO_Init(void);
static void MX_DMA_Init(void);
static void MX_TIM2_Init(void);
static void MX_TIM3_Init(void);
static void MX_TIM4_Init(void);
static void MX_USART1_UART_Init(void);
static void MX_CRC_Init(void);
/* USER CODE BEGIN 0 */

/* Control of LED strips is  based on this idea: https://stm32f4-discovery.net/2018/06/tutorial-control-ws2812b-leds-stm32/ */
/**
 * \brief           Prepares data from memory for PWM output for timer
 * \note            Memory is in format R,G,B, while PWM must be configured in G,R,B
 * \param[in]       ledx: LED index to set the color
 * \param[out]      ptr: Output array with at least LED_CFG_RAW_BYTES_PER_LED-words of memory
 *
 */
static uint8_t led_fill_led_pwm_data(uint8_t ledx, uint32_t* ptr) {
    uint8_t i;

    if (ledx < NR_OF_LEDS) {
        for (i = 0; i < 8; i++) {
            ptr[i] =        (led[ledx] & (1 << (15 - i))) ? (2 * TIM2->ARR / 3) : (TIM2->ARR / 3);
            ptr[8 + i] =    (led[ledx] & (1 << (23 - i))) ? (2 * TIM2->ARR / 3) : (TIM2->ARR / 3);
            ptr[16 + i] =   (led[ledx] & (1 << (7 - i))) ? (2 * TIM2->ARR / 3) : (TIM2->ARR / 3);
        }
        return 1;
    }
    return 0;
}




/**
 * \brief           Update sequence function, called on each DMA transfer complete or half-transfer complete events
 * \param[in]       tc: Transfer complete flag. Set to `1` on TC event, or `0` on HT event
 *
 * \note            TC = Transfer-Complete event, called at the end of block
 * \note            HT = Half-Transfer-Complete event, called in the middle of elements transfered by DMA
 *                  If block is 48 elements (our case),
 *                      HT is called when first LED_CFG_RAW_BYTES_PER_LED elements are transfered,
 *                      TC is called when second LED_CFG_RAW_BYTES_PER_LED elements are transfered.
 *
 * \note            This function must be called from DMA interrupt
 */
void led_update_sequence(uint8_t tc) {
    tc = !!tc;                                  /* Convert to 1 or 0 value only */

    if (current_led < NR_OF_LEDS) {

			current_led++;
			/*
			 *  if there was no TC event (it was HT):
			 *
			 *  - Prepare first part of array, because either there is no transfer
			 *      or second part (from HT to TC) is now in process for PWM transfer
			 *
			 * In other case (TC = 1)
			 */
			if (!tc) {
				led_fill_led_pwm_data(current_led, &tmp_led_data[0]);
			} else {
				led_fill_led_pwm_data(current_led, &tmp_led_data[3*8]);
			}

	/*
	 * When we reached all leds, we have to wait to transmit data for all leds before we can disable DMA and PWM:
	 *
	 *  - If TC event is enabled and we have EVEN number of LEDS (2, 4, 6, ...)
	 *  - If HT event is enabled and we have ODD number of LEDS (1, 3, 5, ...)
	 */
	} else if ((!tc && (NR_OF_LEDS & 0x01)) || (tc && !(NR_OF_LEDS & 0x01))) {
		LL_TIM_CC_DisableChannel(TIM2, LL_TIM_CHANNEL_CH2); /* Disable channel */
		LL_TIM_DisableCounter(TIM2);
		LL_DMA_DisableStream(DMA1, LL_DMA_STREAM_6);
	}
}


/*
 * Process data after UART interrupt: byte received
 */
void handleSerialData() {
	static uint32_t lastTick;
	static uint8_t rxLength; /* number of data bytes to be received. addr&length not counted;  */
	static uint8_t rxByteNr;  /* index of received byte (start with 0) */
	static uint8_t rxAddress; /* node to be addressed, read from first byte */
	static uint8_t nodesSending; /* mode when nodes are sending and Pi is quiet */

	if ( (uwTick - lastTick) > 5 ) /* resync if there was no data for longer than 5 ms */
	{
		rxLength = 0;
		rxByteNr = 0;
		rxAddress = 0;
		nodesSending = 0;
	}
	lastTick = uwTick;


	if ( nodesSending ) {
		rxByteNr++;
		if ( rxByteNr == 2*NODE_ADDRESS ) { /* this node is about to send except if its node 0 */
			nodeStatus = 1;
			rxByteNr += 2;
		}
		if ( rxByteNr == 2*NR_OF_NODES ) { /* all nodes finished sending */
			nodesSending = 0;
			rxByteNr = 0;
		}
	} else {
		if ( rxByteNr == 0 ) {
			rxByteNr++;
			rxLength = currentRx & 0xf; /* get length */
			rxAddress = currentRx>>4;  /* get address */

			if ( rxLength == 0xf ) /* Software update */
			{
				rxLength = 16; /* 16 bytes, that it is a multiple of 4 (good for hardware-CRC calculation) */
				if ( rxAddress == NODE_ADDRESS )
				{
					nodeStatus = 2; /* Software update of this node */
				} else
				{
					nodeStatus = 3;  /* Software update of other node */
				}
			}

			if ( rxAddress == NODE_ADDRESS ) {
				rxBuffer[0] = currentRx;
			}

			if ( (rxAddress == 14) && (nodeStatus != 2) && (nodeStatus != 3) ) {
				if (NODE_ADDRESS == 0) { /* start sending if this is node 0 */
					nodeStatus = 1;
					rxByteNr = 2;
				} else {
					rxByteNr = 0;
				}
				if (NR_OF_NODES > 1) {
					nodesSending = 1; /* more nodes are connected */
				} else {
					rxByteNr = 0;  /* this is the one and only node */
				}
			}
		} else {
			if ( rxAddress == NODE_ADDRESS ) {
				rxBuffer[rxByteNr] = currentRx;
			}
			if (rxByteNr == rxLength) {
				rxByteNr = 0;
				if ( rxAddress == NODE_ADDRESS ) {
					rxBufferUpdated = 1;
				}
			} else {
				rxByteNr++;
			}
		}
	}

}


/* USER CODE END 0 */

/**
  * @brief  The application entry point.
  * @retval int
  */
int main(void)
{
  /* USER CODE BEGIN 1 */

	/* to be started form bootloader, see also
	 * https://embetronicx.com/tutorials/microcontrollers/stm32/bootloader/simple-stm32-bootloader-implementation-bootloader-tutorial/
	 * edit system_stm32f4xx.c as well to enter offset and #define USER_VECT_TAB_ADDRESS
	 * and edit linker script STM32F401CCUX_FLASH.ld */
	__disable_irq();
	SCB->VTOR = 0x8004000;
	__DSB();
	__enable_irq();

  /* USER CODE END 1 */

  /* MCU Configuration--------------------------------------------------------*/

  /* Reset of all peripherals, Initializes the Flash interface and the Systick. */
  HAL_Init();

  /* USER CODE BEGIN Init */
  rxBufferUpdated = 0;
  nodeStatus = 0;

  for (uint8_t bb = 0; bb < 17; bb++)
  {
	  rxBuffer[bb] = 0;
  }

  uint8_t txSwitchesByte1 = 0; /* all switches off */
  uint8_t txSwitchesByte2 = 0;
  uint8_t prevTxSwitchByte1 = 0;
  uint8_t prevTxSwitchByte2 = 0;
  uint8_t txByte1_transmitted = 0;
  uint32_t stReload;
  uint32_t stNow, stOld;
  uint32_t stTicks = 0;
  uint32_t slingPulse = 0;
  uint32_t flipperPulse = 0;
  uint32_t outholePulse = 0;
  uint32_t lockkickPulse = 0;
  uint32_t diverterPulse = 0;
  uint32_t readyToSendCounter = 0;
  uint32_t packetWatchDog = 0;

  /* USER CODE END Init */

  /* Configure the system clock */
  SystemClock_Config();

  /* Initialize all configured peripherals */
  MX_GPIO_Init();
  MX_DMA_Init();
  MX_TIM2_Init();
  MX_TIM3_Init();
  MX_TIM4_Init();
  MX_USART1_UART_Init();
  MX_CRC_Init();
  /* USER CODE BEGIN 2 */

  /* All outputs off */
  LL_TIM_CC_DisableChannel (TIM3, LL_TIM_CHANNEL_CH1);
  LL_TIM_CC_DisableChannel (TIM3, LL_TIM_CHANNEL_CH2);
  LL_TIM_CC_DisableChannel (TIM3, LL_TIM_CHANNEL_CH3);
  LL_TIM_CC_DisableChannel (TIM3, LL_TIM_CHANNEL_CH4);
  LL_TIM_CC_DisableChannel (TIM4, LL_TIM_CHANNEL_CH1);
  LL_TIM_CC_DisableChannel (TIM4, LL_TIM_CHANNEL_CH2);
  LL_TIM_CC_DisableChannel (TIM4, LL_TIM_CHANNEL_CH3);
  LL_TIM_CC_DisableChannel (TIM4, LL_TIM_CHANNEL_CH4);
  LL_TIM_EnableCounter(TIM3);
  LL_TIM_EnableCounter(TIM4);

  stOld = SysTick->VAL;
  stReload = SysTick->LOAD;

  /* USER CODE END 2 */

  /* Infinite loop */
  /* USER CODE BEGIN WHILE */
  while (1)
  {
		/* count systicks. Only works that easy as the while loop is shorter
		 * than 1 ms!! Ohterwise make a systick interrupt or use uwtick (overflow
		 * only after 30 days
		 */
	    stNow = SysTick->VAL;
		if( stNow != stOld )
		{
			if ( stNow < stOld )
			{
				stTicks = (stOld - stNow);
			}
			else
			{
				stTicks = (stReload - stNow + stOld);
			}
			stOld = stNow;
		}

		if(dataArrived)
		{
			dataArrived = 0;
			handleSerialData();
		}

		/* ---------- SW update  ----------- */

		if ( nodeStatus == 3 ) /* Software update of other node */
		{
			  NVIC_DisableIRQ(USART1_IRQn);
			  /* All outputs off */
			  LL_TIM_CC_DisableChannel (TIM3, LL_TIM_CHANNEL_CH1);
			  LL_TIM_CC_DisableChannel (TIM3, LL_TIM_CHANNEL_CH2);
			  LL_TIM_CC_DisableChannel (TIM3, LL_TIM_CHANNEL_CH3);
			  LL_TIM_CC_DisableChannel (TIM3, LL_TIM_CHANNEL_CH4);
			  LL_TIM_CC_DisableChannel (TIM4, LL_TIM_CHANNEL_CH1);
			  LL_TIM_CC_DisableChannel (TIM4, LL_TIM_CHANNEL_CH2);
			  LL_TIM_CC_DisableChannel (TIM4, LL_TIM_CHANNEL_CH3);
			  LL_TIM_CC_DisableChannel (TIM4, LL_TIM_CHANNEL_CH4);
			  LL_TIM_EnableCounter(TIM3);
			  LL_TIM_EnableCounter(TIM4);
			  txSwitchesByte1 = 0; /* all switches off */
			  txSwitchesByte2 = 0;
			  prevTxSwitchByte1 = 0;
			  prevTxSwitchByte2 = 0;
			  LL_GPIO_ResetOutputPin(BlueLED_GPIO_Port, BlueLED_Pin);

	  		  HAL_Delay(20000);
			  NVIC_SystemReset();
		}


		/* write new code to flash and reset */
		if (rxBufferUpdated && (nodeStatus == 2) ) /* Software update */
		{
			uint8_t ww = 0;
			uint32_t loopcounter = 0; /* timer */
			uint8_t blbl = 0; /* blink blink - so oft wird geblinkt */
			uint32_t writeAddress = 0x08020000; /* begin of sector 5 */
			HAL_FLASH_Unlock();

			while (1)
			{
				if(dataArrived)
				{
					dataArrived = 0;
					handleSerialData();
				}

				if (rxBufferUpdated && (nodeStatus == 2) )
				{
					rxBufferUpdated = 0;
					loopcounter = 0;
					LL_GPIO_TogglePin (GPIOC, LL_GPIO_PIN_13);
					for (ww = 0; ww < 16; ww++)
					{
						HAL_FLASH_Program(FLASH_TYPEPROGRAM_BYTE, writeAddress, ((uint8_t *)(rxBuffer+1))[ww] );
						writeAddress++;
					}
				}
				loopcounter++;
				if ( loopcounter > 3000000 ) /* ganz grob eine Sekunde */
				{
					LL_GPIO_TogglePin (GPIOC, LL_GPIO_PIN_13);
					loopcounter = 0;
					blbl++;
				}
				if (blbl == 6) NVIC_SystemReset();
			}
		}
		/* ---------- SW update end ----------- */

		if (rxBufferUpdated)
		{
		  LL_GPIO_TogglePin (GPIOC, LL_GPIO_PIN_13);
		  rxBufferUpdated = 0;
		  packetWatchDog = 0;

		  led[0] = ((rxBuffer[2]>>7)&1) ? BLACK : BLACK; /* nc */
		  led[1] = ((rxBuffer[2]>>6)&1) ? WHITE : BLACK; /* GI */
		  led[2] = ((rxBuffer[2]>>5)&1) ? WHITE : BLACK; /* GI */
		  led[3] = ((rxBuffer[2]>>4)&1) ? RED : BLACK;
		  led[4] = ((rxBuffer[2]>>3)&1) ? YELLOW : BLACK;
		  led[5] = ((rxBuffer[2]>>2)&1) ? GREEN : BLACK;
		  led[6] = ((rxBuffer[2]>>1)&1) ? BLACK : BLACK; /* nc */
		  led[7] = ((rxBuffer[2]>>0)&1) ? ORANGE : BLACK;

		  led[8] = ((rxBuffer[3]>>7)&1) ? RED : BLACK;
		  led[9] = ((rxBuffer[3]>>6)&1) ? GREEN : BLACK;
		  led[10] = ((rxBuffer[3]>>5)&1) ? GREEN : BLACK;
		  led[11] = ((rxBuffer[3]>>4)&1) ? GREEN : BLACK;
		  led[12] = ((rxBuffer[3]>>3)&1) ? GREEN : BLACK;
		  led[13] = ((rxBuffer[3]>>2)&1) ? GREEN : BLACK;
		  led[14] = ((rxBuffer[3]>>1)&1) ? RED : BLACK;
		  led[15] = ((rxBuffer[3]>>0)&1) ? RED : BLACK;

		  led[16] = ((rxBuffer[4]>>7)&1) ? ORANGE : BLACK;
		  led[17] = ((rxBuffer[4]>>6)&1) ? RED : BLACK;
		  led[18] = ((rxBuffer[4]>>5)&1) ? RED : BLACK;
		  led[19] = ((rxBuffer[4]>>4)&1) ? RED : BLACK;
		  led[20] = ((rxBuffer[4]>>3)&1) ? BLACK : BLACK;
		  led[21] = ((rxBuffer[4]>>2)&1) ? RED : BLACK;
		  led[22] = ((rxBuffer[4]>>1)&1) ? RED : BLACK;
		  led[23] = ((rxBuffer[4]>>0)&1) ? RED : BLACK;

		  led[24] = ((rxBuffer[5]>>7)&1) ? RED : BLACK;
		  led[25] = ((rxBuffer[5]>>6)&1) ? RED : BLACK;
/*		  led[26] = ((rxBuffer[5]>>5)&1) ? WHITE : BLACK;*/
		  if ((rxBuffer[5]>>5)&1) led[26] = WHITE;
		  else if ((rxBuffer[7]>>0)&1) led[26] = RED;
		  else if ((rxBuffer[8]>>7)&1) led[26] = YELLOW;
		  else if ((rxBuffer[8]>>6)&1) led[26] = GREEN;
		  else led[26] = BLACK;
		  led[27] = ((rxBuffer[5]>>4)&1) ? RED : BLACK;
		  led[28] = ((rxBuffer[5]>>3)&1) ? WHITE : BLACK;
		  led[29] = ((rxBuffer[5]>>2)&1) ? RED : BLACK;
/*		  led[30] = ((rxBuffer[5]>>1)&1) ? WHITE : BLACK;*/
		  if ((rxBuffer[5]>>5)&1) led[30] = WHITE;
		  else if ((rxBuffer[7]>>0)&1) led[30] = RED;
		  else if ((rxBuffer[8]>>7)&1) led[30] = YELLOW;
		  else if ((rxBuffer[8]>>6)&1) led[30] = GREEN;
		  else led[30] = BLACK;
		  led[31] = ((rxBuffer[5]>>0)&1) ? RED : BLACK;

		  led[32] = ((rxBuffer[6]>>7)&1) ? RED : BLACK;
		  led[33] = ((rxBuffer[6]>>6)&1) ? RED : BLACK;
		  led[34] = ((rxBuffer[6]>>5)&1) ? WHITE : BLACK;
		  led[35] = ((rxBuffer[6]>>4)&1) ? WHITE : BLACK;
		  led[36] = ((rxBuffer[6]>>3)&1) ? WHITE : BLACK;
		  led[37] = ((rxBuffer[6]>>2)&1) ? RED : BLACK;
		  led[38] = ((rxBuffer[6]>>1)&1) ? RED : BLACK;
		  led[39] = ((rxBuffer[6]>>0)&1) ? RED : BLACK;

		  led[40] = ((rxBuffer[7]>>7)&1) ? RED : BLACK;
		  led[41] = ((rxBuffer[7]>>6)&1) ? RED : BLACK;
		  led[42] = ((rxBuffer[7]>>5)&1) ? RED : BLACK;
		  led[43] = ((rxBuffer[7]>>4)&1) ? WHITE : BLACK;
		  led[44] = ((rxBuffer[7]>>3)&1) ? WHITE : BLACK;
		  led[45] = ((rxBuffer[7]>>2)&1) ? WHITE : BLACK;
		  led[46] = ((rxBuffer[7]>>1)&1) ? WHITE : BLACK;
		  led[47] = ((rxBuffer[7]>>0)&1) ? RED : BLACK; // Dummy LED

		  led[48] = ((rxBuffer[8]>>7)&1) ? YELLOW : BLACK; // Dummy LED
		  led[49] = ((rxBuffer[8]>>6)&1) ? GREEN : BLACK; // Dummy LED

		  current_led = 0;
		  led_fill_led_pwm_data(current_led, &tmp_led_data[0]); /* first LED */
		  current_led++;
		  led_fill_led_pwm_data(current_led, &tmp_led_data[3*8]); /* second LED */

	      LL_DMA_ClearFlag_TC6(DMA1);
	      LL_DMA_ClearFlag_HT6(DMA1);
	      LL_DMA_EnableStream(DMA1, LL_DMA_STREAM_6);
	      LL_TIM_SetCounter (TIM2, 0);
	      LL_TIM_EnableCounter(TIM2);
	      LL_TIM_CC_EnableChannel(TIM2, LL_TIM_CHANNEL_CH2);

			/* Set and reset outputs (solenoids, magnets, flashers) */
			/* OB8 */
			/* OB8 -> right flipper controlled by flipper button. Pi only enables flipper generally (e.g. not tilt)
			((rxBuffer[1]>>7)&1) ?
				LL_TIM_CC_EnableChannel (TIM4, LL_TIM_CHANNEL_CH3) : LL_TIM_CC_EnableChannel (TIM4, LL_TIM_CHANNEL_CH3);*/
			/* OB9 */
	        /* magnet not used in JD */
			/*((rxBuffer[1]>>6)&1) ?
				LL_TIM_CC_EnableChannel (TIM4, LL_TIM_CHANNEL_CH4) : LL_TIM_CC_DisableChannel (TIM4, LL_TIM_CHANNEL_CH4);*/
			/* OB1 */
			/* outhole kicker controlled directly */
			/*((rxBuffer[1]>>5)&1) ?
				LL_TIM_CC_EnableChannel (TIM3, LL_TIM_CHANNEL_CH4) : LL_TIM_CC_DisableChannel (TIM3, LL_TIM_CHANNEL_CH4);*/
			/* OB6 */
			((rxBuffer[1]>>4)&1) ?
				LL_TIM_CC_EnableChannel (TIM4, LL_TIM_CHANNEL_CH1) : LL_TIM_CC_DisableChannel (TIM4, LL_TIM_CHANNEL_CH1);
			/* OB7 */
			/* OB7 -> right sling shot controlled by switch -> see later in code. Pi only enables sling generally */
			/*((rxBuffer[1]>>3)&1) ?
				LL_TIM_CC_EnableChannel (TIM4, LL_TIM_CHANNEL_CH2) : LL_TIM_CC_DisableChannel (TIM4, LL_TIM_CHANNEL_CH2);*/
			/* OA6 */
			/* Lock diverter controlled directly  */
			/*((rxBuffer[1]>>2)&1) ?
				LL_TIM_CC_EnableChannel (TIM3, LL_TIM_CHANNEL_CH1) : LL_TIM_CC_DisableChannel (TIM3, LL_TIM_CHANNEL_CH1);*/
			/* OA7 */
			/* Lock kickback controlled directly */
			/*((rxBuffer[1]>>1)&1) ?
				LL_TIM_CC_EnableChannel (TIM3, LL_TIM_CHANNEL_CH2) : LL_TIM_CC_DisableChannel (TIM3, LL_TIM_CHANNEL_CH2);*/
			/* OB0 */
			((rxBuffer[1]>>0)&1) ?
				LL_TIM_CC_EnableChannel (TIM3, LL_TIM_CHANNEL_CH3) : LL_TIM_CC_DisableChannel (TIM3, LL_TIM_CHANNEL_CH3);

		}

	    /* Poll switches and remember if they where activated until they are reset to 0 with
	     * after sent to Pi */
		txSwitchesByte1 |= (
			    LL_GPIO_IsInputPinSet (GPIOA, LL_GPIO_PIN_8)<<7 |
				LL_GPIO_IsInputPinSet (GPIOA, LL_GPIO_PIN_5)<<6 |
				LL_GPIO_IsInputPinSet (GPIOA, LL_GPIO_PIN_4)<<5 |
				LL_GPIO_IsInputPinSet (GPIOA, LL_GPIO_PIN_3)<<4 |
				LL_GPIO_IsInputPinSet (GPIOA, LL_GPIO_PIN_2)<<3 |
				LL_GPIO_IsInputPinSet (GPIOA, LL_GPIO_PIN_1)<<2 |
				LL_GPIO_IsInputPinSet (GPIOB, LL_GPIO_PIN_13)<<1 |
				LL_GPIO_IsInputPinSet (GPIOB, LL_GPIO_PIN_12));
		txSwitchesByte2 |= (
				LL_GPIO_IsInputPinSet (GPIOB, LL_GPIO_PIN_10)<<7 |
				LL_GPIO_IsInputPinSet (GPIOB, LL_GPIO_PIN_5)<<6 |
				LL_GPIO_IsInputPinSet (GPIOB, LL_GPIO_PIN_4)<<5 |
				LL_GPIO_IsInputPinSet (GPIOA, LL_GPIO_PIN_15)<<4 |
				LL_GPIO_IsInputPinSet (GPIOC, LL_GPIO_PIN_15)<<3 |
				LL_GPIO_IsInputPinSet (GPIOC, LL_GPIO_PIN_14)<<2 |
				LL_GPIO_IsInputPinSet (GPIOB, LL_GPIO_PIN_15)<<1 |
				LL_GPIO_IsInputPinSet (GPIOB, LL_GPIO_PIN_14));


		/* set fast solenoids (controlled solenoids by stwitch) */

		/* right flipper Button pressed and enabled, don't use
		 * txSwitchesByte1 here (as they stay 1 until transferred to Pi) */
		if ( LL_GPIO_IsInputPinSet (GPIOA, LL_GPIO_PIN_1) && ((rxBuffer[1]>>7)&1) )
		{
			LL_TIM_CC_EnableChannel (TIM4, LL_TIM_CHANNEL_CH3);
			LL_TIM_CC_DisableChannel (TIM4, LL_TIM_CHANNEL_CH4); /* magnet off */
		}
		else
		{
			if (flipperPulse > 420000) /* minimum on time is 5 ms to debounce flipper button (if it bounces the flipper doesn't get full power) */
			{
				LL_TIM_CC_DisableChannel (TIM4, LL_TIM_CHANNEL_CH3);
				flipperPulse = 0;
			}
		}
		if ( LL_TIM_CC_IsEnabledChannel(TIM4, LL_TIM_CHANNEL_CH3) ) flipperPulse += stTicks;

		/* rising edge of right sling shot switch */
		if ( ((txSwitchesByte2>>7)&1) && !((prevTxSwitchByte2>>7)&1) && ((rxBuffer[1]>>3)&1) && !slingPulse )
		{
			slingPulse = 1;
			LL_TIM_CC_EnableChannel (TIM4, LL_TIM_CHANNEL_CH2);
		}
		if ( slingPulse ) slingPulse += stTicks;
		if ( slingPulse > 3360000 ) LL_TIM_CC_DisableChannel (TIM4, LL_TIM_CHANNEL_CH2); /* 40 ms @ 84 MHz */
		if ( slingPulse > 33600000 ) slingPulse = 0; /* anti bouncing 400 ms @ 84 MHz */

		/* outhole switch active */
		if ( ((txSwitchesByte2>>1)&1) && !outholePulse )
		{
			outholePulse = 1;
			LL_TIM_CC_EnableChannel (TIM3, LL_TIM_CHANNEL_CH4);
		}
		if ( outholePulse ) outholePulse += stTicks;
		if ( outholePulse > 3360000 ) LL_TIM_CC_DisableChannel (TIM3, LL_TIM_CHANNEL_CH4); /* 40 ms @ 84 MHz */
		if ( outholePulse > 168e6 ) outholePulse = 0; /* anti bouncing 2 s @ 84 MHz */

		/* Lock 1 switch active */
		if ( ((txSwitchesByte1>>1)&1) && !lockkickPulse )
		{
			lockkickPulse = 1;
			LL_TIM_CC_EnableChannel (TIM3, LL_TIM_CHANNEL_CH2);
		}
		if ( lockkickPulse ) lockkickPulse += stTicks;
		if ( lockkickPulse > 3360000 ) LL_TIM_CC_DisableChannel (TIM3, LL_TIM_CHANNEL_CH2); /* 40 ms @ 84 MHz */
		if ( lockkickPulse > 168e6 ) lockkickPulse = 0; /* anti bouncing 2 s @ 84 MHz */

		/* Ramp Lock Entry switch active */
		if ( ((rxBuffer[8]>>5)&1) && !diverterPulse )
		{
			diverterPulse = 1;
			LL_TIM_CC_EnableChannel (TIM3, LL_TIM_CHANNEL_CH1);
		}
		if ( diverterPulse ) lockkickPulse += stTicks;
		if ( diverterPulse > 3360000 ) LL_TIM_CC_DisableChannel (TIM3, LL_TIM_CHANNEL_CH1); /* 40 ms @ 84 MHz */
		if ( diverterPulse > 168e6 ) diverterPulse = 0; /* anti bouncing 2 s @ 84 MHz */


		/* send status to Pi, currently only switch states */
		if ( nodeStatus == 1 )
		{
			/* wait a little (minimum half a bit with) to be sure that TransmitComplete of previous node
			 * is done and RS485 bus is free */
			if ( readyToSendCounter > 4200 ) /* 50 µs @ 84 MHz */
			{
				if ( LL_USART_IsActiveFlag_TXE(USART1) && (!txByte1_transmitted) )
				{
					LL_GPIO_SetOutputPin (GPIOA, RS485_nWrite_Pin);
					LL_USART_TransmitData8 (USART1, txSwitchesByte1);
					txByte1_transmitted = 1;
				}
				if ( LL_USART_IsActiveFlag_TXE(USART1) && txByte1_transmitted ) {
						LL_USART_TransmitData8 (USART1, txSwitchesByte2);
						nodeStatus = 0;
						txByte1_transmitted = 0;
						readyToSendCounter = 0;
						txSwitchesByte1 = 0;
						txSwitchesByte2 = 0;
				}
			}
			readyToSendCounter += stTicks;

			/* Timeout SENDING Status after 5 ms @ 84 MHz */
			if ( readyToSendCounter > 420000 )
			{
				nodeStatus = 0;
				readyToSendCounter = 0;
				txByte1_transmitted = 0;
			}
		}

		prevTxSwitchByte1 = txSwitchesByte1; /* for edge detection */
		prevTxSwitchByte2 = txSwitchesByte2;


		/* Paketintervall-Überwachung*/
		packetWatchDog += stTicks;
		/* toggle LED after 4 seconds */
		if ( packetWatchDog > 336000000 ) LL_GPIO_TogglePin (GPIOC, LL_GPIO_PIN_13);
		/* Timeout WatchDog: 5 s @ 84 MHz */
		if ( packetWatchDog > 420000000 )
		{
			NVIC_SystemReset();
		}

  }
    /* USER CODE END WHILE */

}

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


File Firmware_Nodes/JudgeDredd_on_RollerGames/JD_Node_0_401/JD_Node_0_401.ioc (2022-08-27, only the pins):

Mcu.UserName=STM32F401CCUx
PA0-WKUP.GPIO_Label=KeySwitch
PA0-WKUP.Signal=GPIO_Input
PA1.Signal=GPIO_Input
PA10.Signal=USART1_RX
PA11.Signal=S_TIM1_CH4
PA12.GPIO_Label=RS485_nWrite
PA12.Signal=GPIO_Output
PA13.Signal=SYS_JTMS-SWDIO
PA14.Signal=SYS_JTCK-SWCLK
PA15.Signal=GPIO_Input
PA2.Signal=GPIO_Input
PA3.Signal=GPIO_Input
PA4.Signal=GPIO_Input
PA5.Signal=GPIO_Input
PA6.Signal=S_TIM3_CH1
PA7.Signal=S_TIM3_CH2
PA8.Signal=GPIO_Input
PA9.Signal=USART1_TX
PB0.Signal=S_TIM3_CH3
PB1.Signal=S_TIM3_CH4
PB10.Signal=GPIO_Input
PB12.Signal=GPIO_Input
PB13.Signal=GPIO_Input
PB14.Signal=GPIO_Input
PB15.Signal=GPIO_Input
PB3.Signal=S_TIM2_CH2
PB4.Signal=GPIO_Input
PB5.Signal=GPIO_Input
PB6.Signal=S_TIM4_CH1
PB7.Signal=S_TIM4_CH2
PB8.Signal=S_TIM4_CH3
PB9.Signal=S_TIM4_CH4
PC13-ANTI_TAMP.GPIO_Label=BlueLED
PC13-ANTI_TAMP.Signal=GPIO_Output
PC14-OSC32_IN.Signal=GPIO_Input
PC15-OSC32_OUT.Signal=GPIO_Input

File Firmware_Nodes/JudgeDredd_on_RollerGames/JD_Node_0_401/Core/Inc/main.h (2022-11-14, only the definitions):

#define SOLFORCE25 4300
#define SOLFORCE50 7500
#define BlueLED_Pin LL_GPIO_PIN_13
#define BlueLED_GPIO_Port GPIOC
#define KeySwitch_Pin LL_GPIO_PIN_0
#define KeySwitch_GPIO_Port GPIOA
#define RS485_nWrite_Pin LL_GPIO_PIN_12
#define RS485_nWrite_GPIO_Port GPIOA
#define NODE_ADDRESS 0 /* this nodes address */
#define NR_OF_NODES 3 /* total number of nodes in system */
#define NR_OF_LEDS 50 /* 47 + 3xDummy, number of LEDs on the LED-string connected to this node */
#define BLACK       0x000000
#define MAROON      0x800000
#define DARKGREEN   0x008000
#define OLIVE       0x808000
#define NAVY        0x000080
#define PURPLE      0x800080
#define TEAL        0x008080
#define GREY        0x808080
#define RED         0xff0000
#define GREEN       0x00ff00
#define YELLOW      0xffff00
#define BLUE        0x0000ff
#define MAGENTA     0xff00ff
#define AQUA        0x00ffff
#define WHITE       0xffffff
#define ORANGE		0xff4000

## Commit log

2022-08-27 added Hardware_Nodes
    [RTMPin-B_Cu.gbl, RTMPin-B_Mask.gbs, RTMPin-B_Paste.gbp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]
2022-09-01 added schematic_RTMpin.pdf
2022-09-30 HW bugfix
    [RTMPin.kicad_pcb, RTMPin.sch]
2022-09-30 Schematic pdf updated
2022-10-01 all parts on top side
    [RTMPin.kicad_pcb, RTMPin.sch]
2022-10-02 rm Gerber
    [RTMPin-B_Cu.gbl, RTMPin-B_Mask.gbs, RTMPin-B_Paste.gbp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]
2022-10-02 rm xsl added BOM
    [RTMPin-B_Cu.gbl, RTMPin-B_Mask.gbs, RTMPin-B_Paste.gbp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]
2022-10-03 tvs unipolar
    [RTMPin.kicad_pcb, RTMPin.sch, RTMPin_BOM.csv]
2022-10-29 added JD
    [JD_Mapping.ods, RG_Mapping.ods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]
2022-10-29 updated .gitignore
    [RTMPin-NPTH.drl, RTMPin-PTH.drl, RTMPin-bottom-pos.csv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]
2022-11-14 fixed update and debounce flipper
    [main.c]
2022-11-14 fix update in JDonRG
    [main.c]
2022-11-19 JD special functions
    [JD_Mapping.ods]

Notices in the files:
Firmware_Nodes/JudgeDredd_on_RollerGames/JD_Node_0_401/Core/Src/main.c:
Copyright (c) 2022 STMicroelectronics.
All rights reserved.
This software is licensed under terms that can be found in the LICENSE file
